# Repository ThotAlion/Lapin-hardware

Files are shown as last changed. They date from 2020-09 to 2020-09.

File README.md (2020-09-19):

# Lapin-hardware
---
# Hardware of the lapin biped robot

Here is gathered the hardware of the robot, and the BOM. This can change during the search on this robot
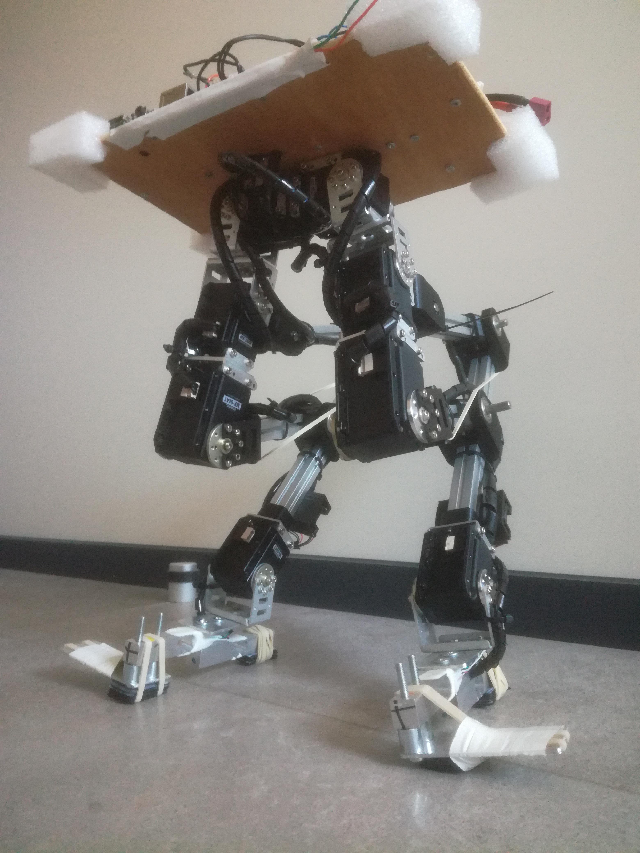
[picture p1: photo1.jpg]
Overview


---

## Mechanical constraints and golden rules

**Golden rule 1 :** A dynamic biped robot shall fall without breaking. Systems which hold the robot for security disturb the dynamics

**Golden rule 2 :** A dynamic biped robot shall be stable around twist axis. If a torque is applied around the vertical axis while the robot is standing, the gripping of the feet shall prevent turning

**Golden rule 3 :** A dynamic biped robot shall have the gravity center the higher to increase the natural period of the balancing.

---

## Bunch of material

Here is the bunch of material for my robot but it can be adapted for yours.

### Motors

The robot need high torque and high quality motors for research purpose.Maybe later it can be useful to reduce motor costs but for now, make it walk. Moreover, these motors can be used for others future projects.

- 2 x Dynamixel [MX-64AT](http://www.robotis.us/dynamixel-mx-64at/) 262€ each
- 6 x Dynamixel [MX-28AT](http://www.robotis.us/dynamixel-mx-28at/) 203€ each
- 2 x U frame for MX-64 with bearing [FR05-H101 Set](http://www.robotis.us/fr05-h101-set/) 25€ each
- 6 x U frame for MX-28 with bearing [FR07-H101 Set](http://www.robotis.us/fr07-h101-set/) 24€ each
- 4 x plates for MX-28 [FR07-S101](http://www.robotis.us/fr07-s101-set/) 10€ each
- 2 x plates for MX-64 [FR05-S101](http://www.robotis.us/fr05-s101-set/) 13€ each
- Dynamixel USB controller [U2D2](http://www.robotis.us/u2d2/) or [USB2AX](https://www.generationrobots.com/fr/401584-usb2ax-pour-servomoteurs-dynamixel.html)
- 2 x sets of 100mm Dynamixel [3P cables(x 10)](http://www.robotis.us/robot-cable-3p-100mm-10pcs/)
- 1 custom Y dynamixel cable from the dynamixel controller to the two legs (avoid dynamixel hub because of the schocks)
- 2 x custom dynamixel cables of 350mm from MX-64 knee to MX-28 ankle

### Power
- 1 x 3S LIPO battery
- 1 x [kit of male/female T-connectors](https://fr.aliexpress.com/item/4001351319074.html)
- 1 x 10A Emergency stop button
- 1 x [25W switching regulator](https://www.robotshop.com/eu/fr/regulateur-de-swadj3-dimension-engineering.html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)

### Computer

- 1 x Raspberry Pi 3 or 4
- 1 x 16Go SDCard

### Sensors

The robot is sensitive to ground contact and inertial measurement with a high rate and high speed (approach 100Hz). All is gathered around a dedicated Arduino.

- 1 x Arduino 
  - [Nano 3.0](https://store.arduino.cc/arduino-nano)
  - [Nano Every](https://store.arduino.cc/arduino-nano-every-with-headers) even if I have problem of I²C stability on this card to be investigated with respect to MPU6050 (spurious freeze)
- 1 x I²C IMU 
  - for the moment I use [INVENSENSE MPU6050](https://fr.aliexpress.com/item/32670910753.html) but I have software stability issue using the embedded DMP 
  -  [BOSCH BNO055](https://fr.aliexpress.com/item/4000686420656.html) on its way to test

- 4 x [5kg force sensor beams with HX711 A2D converter](https://fr.aliexpress.com/item/33046501052.html)
- 2 x [3D printed HX711 housing](https://cad.onshape.com/documents/89773ebe7e884f666a84c098/w/31c162daa679029f3b9fda3b/e/070fb8623ed9564c90b82de8)
- 1 x [band of 15 Neopixel WS2812 - 1M 60 IP30](https://fr.aliexpress.com/item/2036819167.html)

### mechanical leg structure

All 3D printed parts are designed on OnShape in [this project](https://cad.onshape.com/documents/fe91fe1ed7270e269f4c2873/w/a1669b9394a00a6c775fa6e8/e/9fc7b1788347e23db4327b82).
STLfiles have been exported in this repo.

- 2 x [1m long Makerbeam XL](https://www.makerbeam.com/1000mm-1p-makerbeamxl-15mmx15mm.html)
- 1 x [kit of Makerbeam bolts](https://www.makerbeam.com/openbeam-button-head-socket-bolt-6mm-100p-for-open.html)
- 1 x [kit of slot nuts](https://www.makerbeam.com/t-slot-nuts-for-makerbeamxl-50p.html)
- 12 bearings Inner diameter : 6mm, outer diameter 19mm, thickness : 6mm
- 6 x 6mm diameter 40mm long steel axes
- 4 x 3D printed makerbeamXL outerhinge
- 6 x 3D printed makerbeamXL innerhinge
- 2 x 3D printed makerbeamXL outerhingeplate
- 4 x 3D printed makerbeamXL headplate
- 1 x kit of standard kitchen rubber bands diameter : 50mm, thickness : 5mm

### foot

work in progress

### around
- 1 x [spiral wire protection 6mm diameter x 15m long](https://fr.aliexpress.com/item/4001090365450.html) to handle schocks and prevent wire cut during fall
- 1 x [kit of female connectors over PCB](https://fr.aliexpress.com/item/32983464320.html)
- 1 x [kit of female/male connectors over wires](https://fr.aliexpress.com/item/32960322306.html)

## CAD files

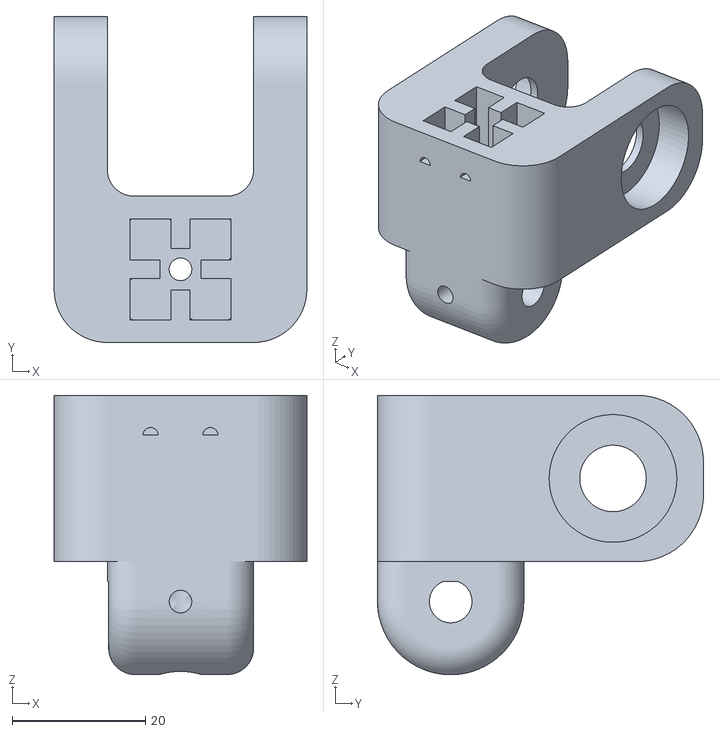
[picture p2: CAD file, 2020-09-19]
3D stl parts/headplate.stl
38.0 x 49.0 x 42.0

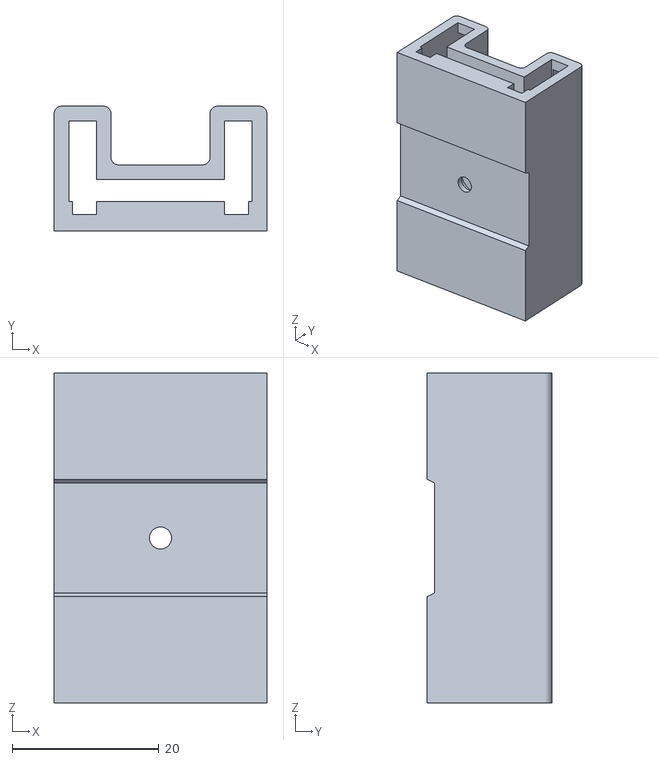
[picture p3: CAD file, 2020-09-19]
3D stl parts/hx711box.stl
29.0 x 17.0 x 45.0

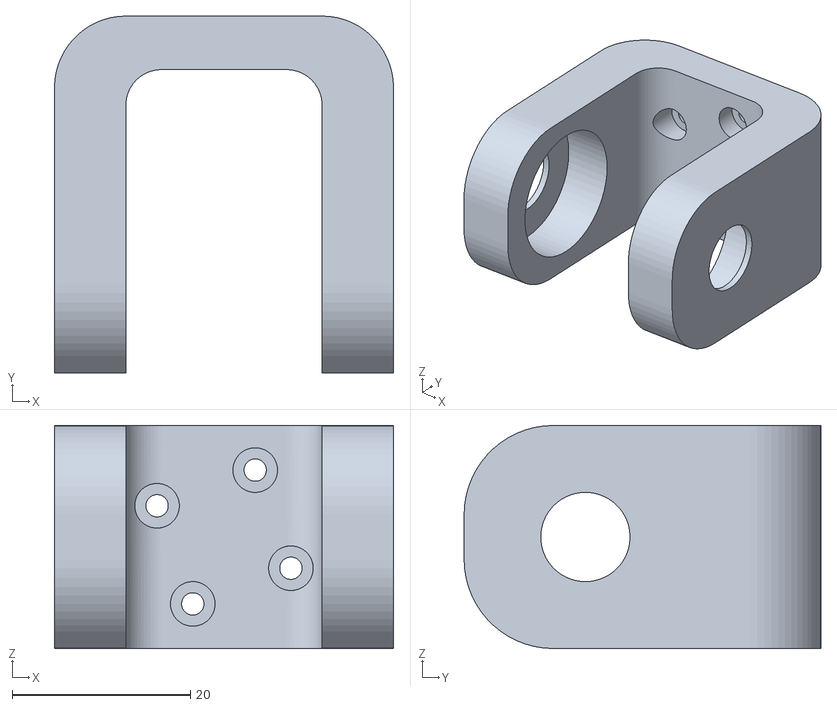
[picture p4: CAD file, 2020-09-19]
3D stl parts/outerhingeplate.stl
38.0 x 40.0 x 25.0
